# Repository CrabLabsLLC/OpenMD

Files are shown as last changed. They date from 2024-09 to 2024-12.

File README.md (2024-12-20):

# OpenMD

An Open Source Versatile Motor Driver powered by GaN

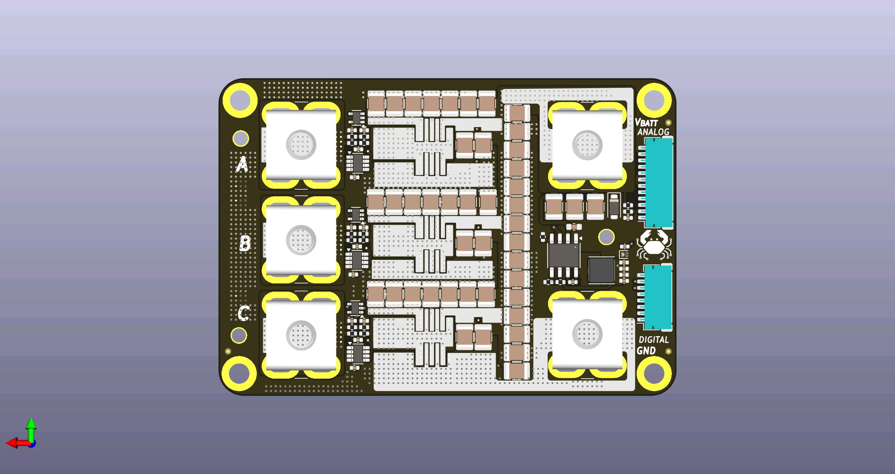
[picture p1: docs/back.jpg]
Back

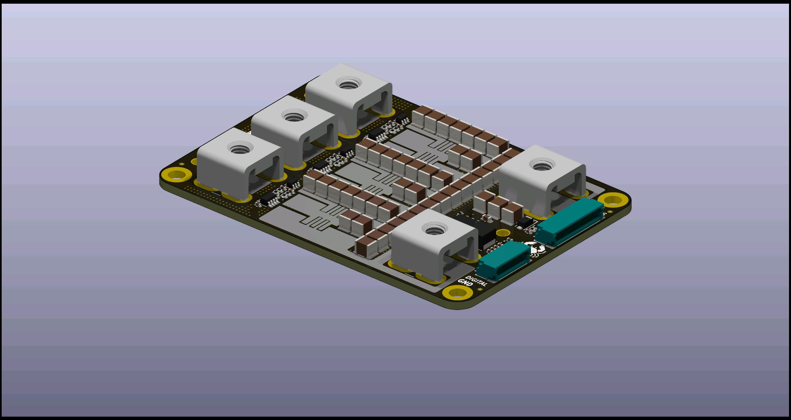
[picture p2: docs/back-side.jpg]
Side Back

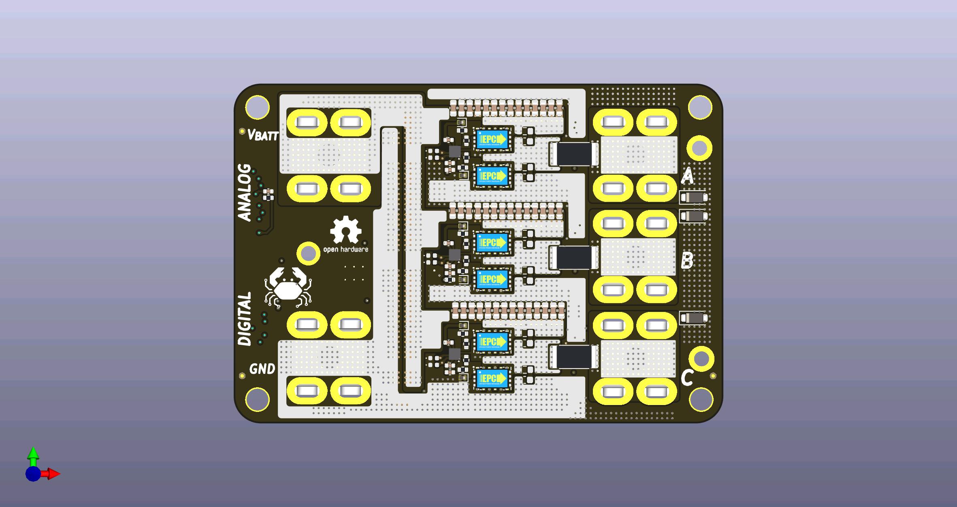
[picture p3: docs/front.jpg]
Front

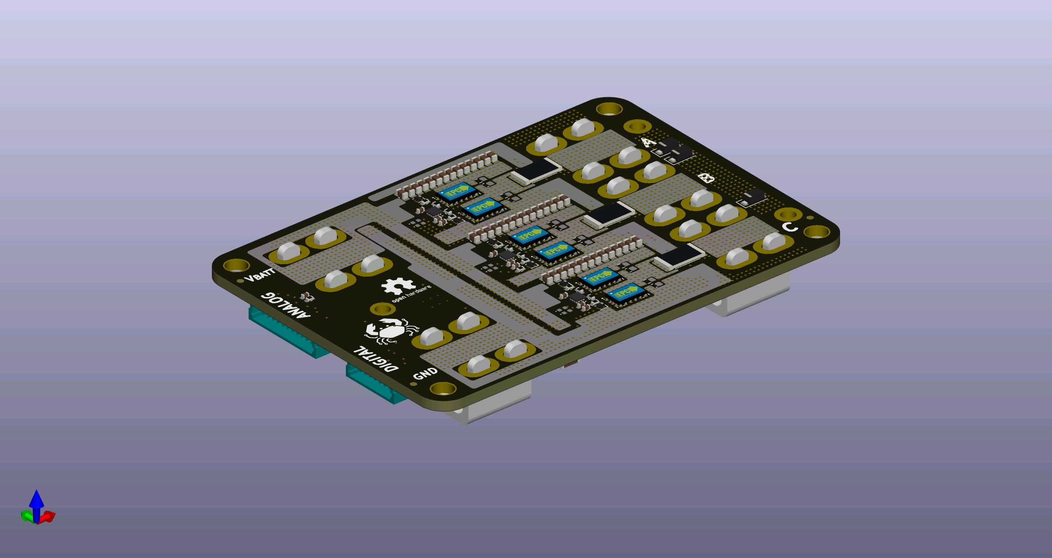
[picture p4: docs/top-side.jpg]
Side Front


## Authors

[Orion Serup](orion@crablabs.io)

## Licensing

This project is licensed under the CERN Open Hardware License Version 2 - Weakly Reciprocal.

Different licensing can be provided for a nominal fee to allow for private spins of the design, contact the authors for more information on cost and license options.

## Operational Parameters

These are the initial estimates for reasonable limits provided sufficient cooling and stable power.

- Operating Voltage: 7V-80V
- Operating Current: 70A
- Max Theoretical Power: 4kW
- Switching Frequency: 50kHz-150KHz

## Purchasing

As of now this product is in Beta and thus is not publicly available for sale. Pre-production units may be available for evaluation, contact the authors for more information.

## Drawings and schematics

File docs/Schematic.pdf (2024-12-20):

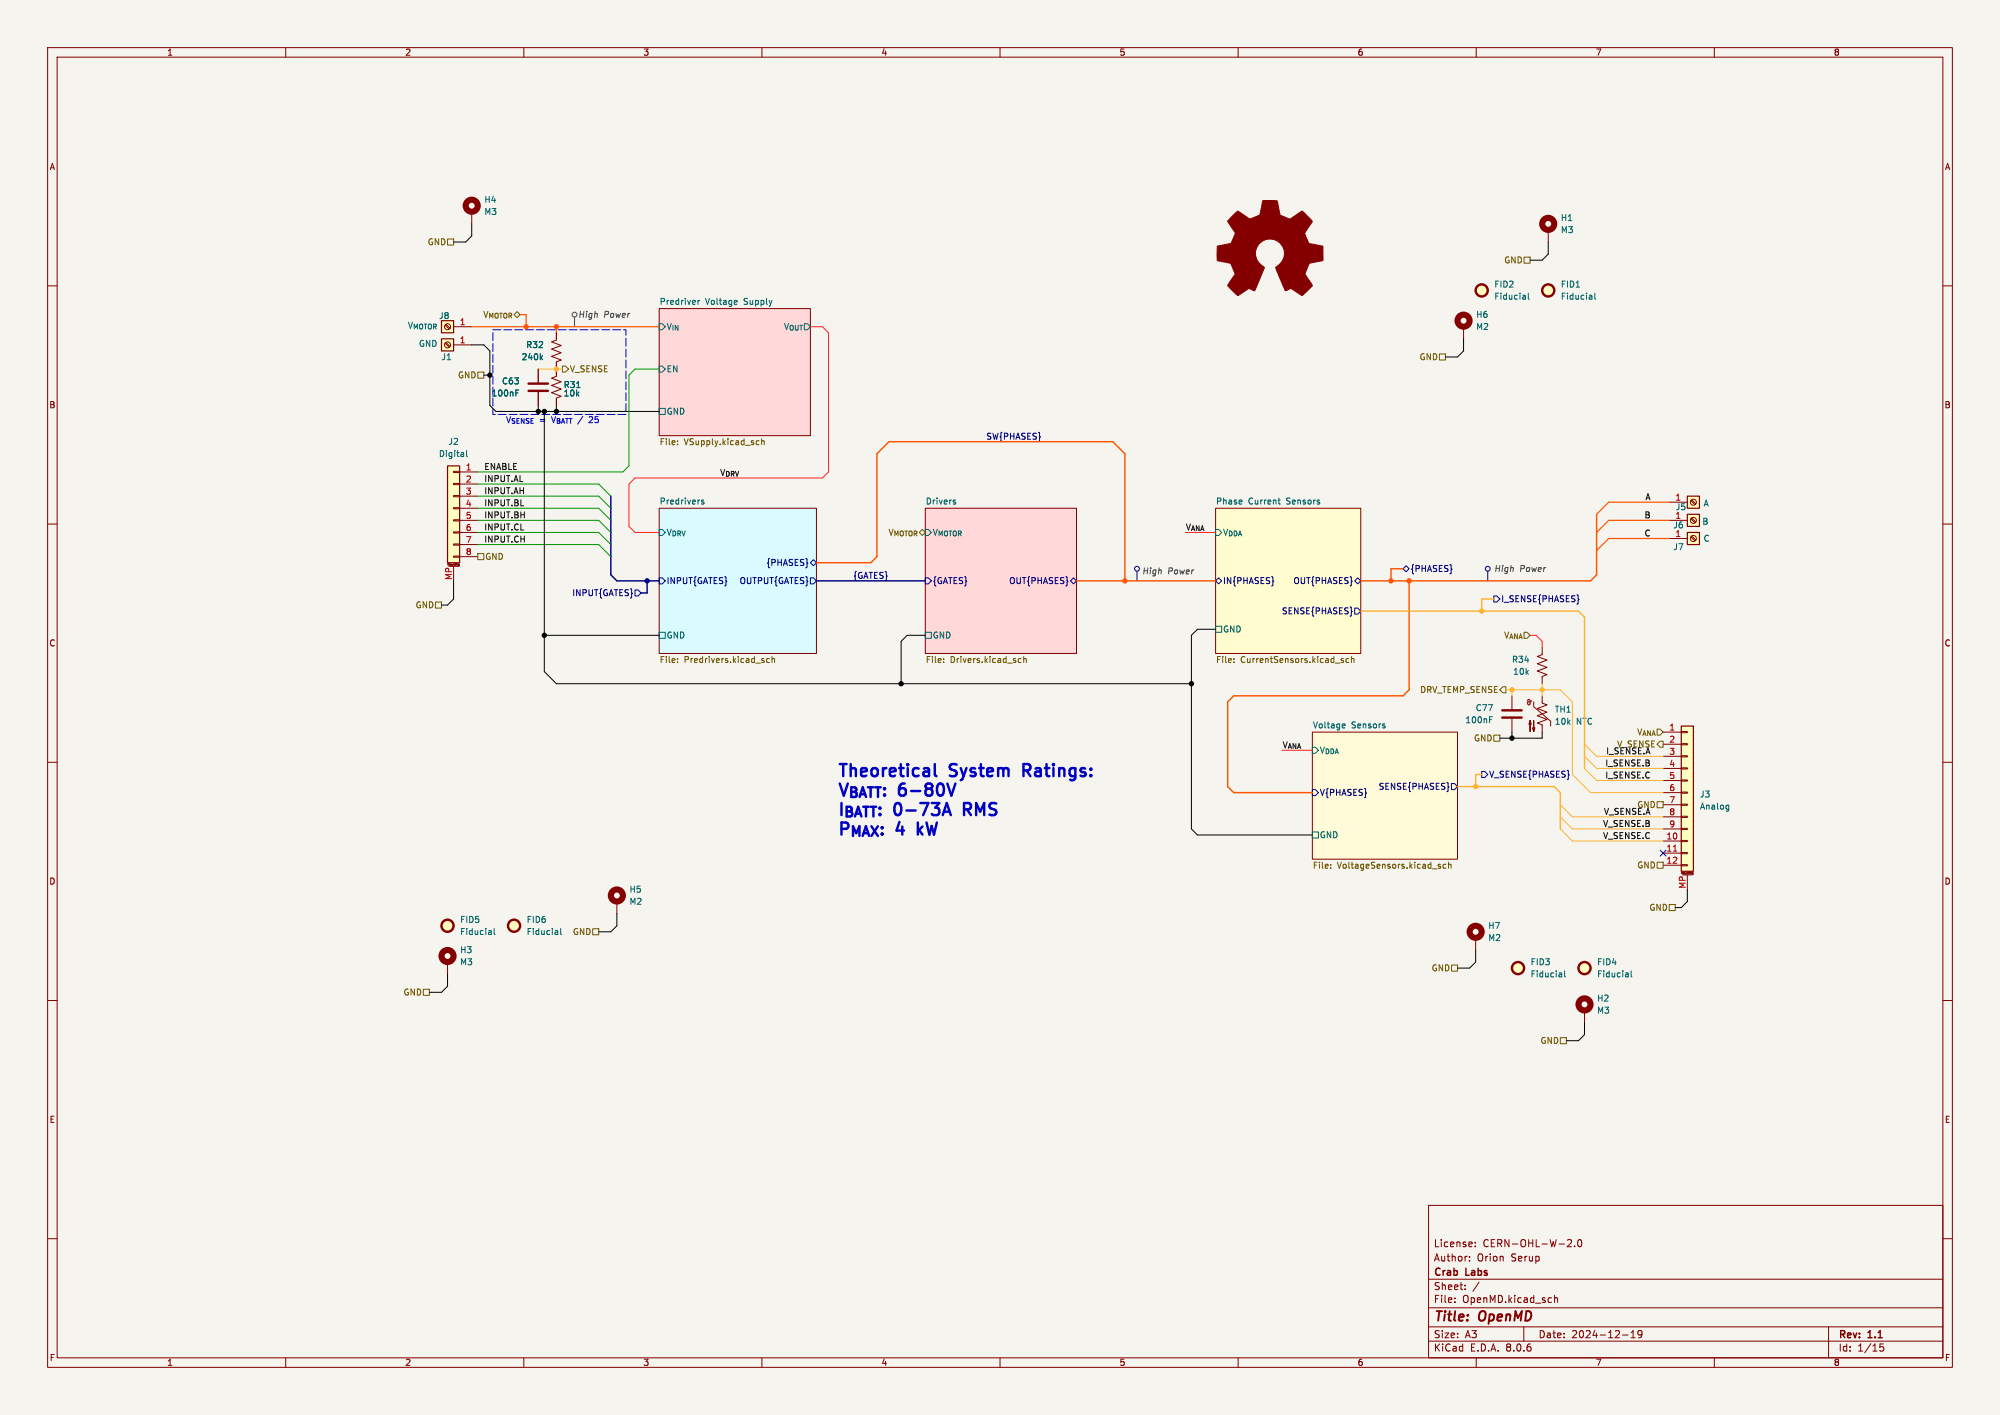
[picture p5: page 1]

Voltage Sensors File: VoltageSensors.kicad_sch

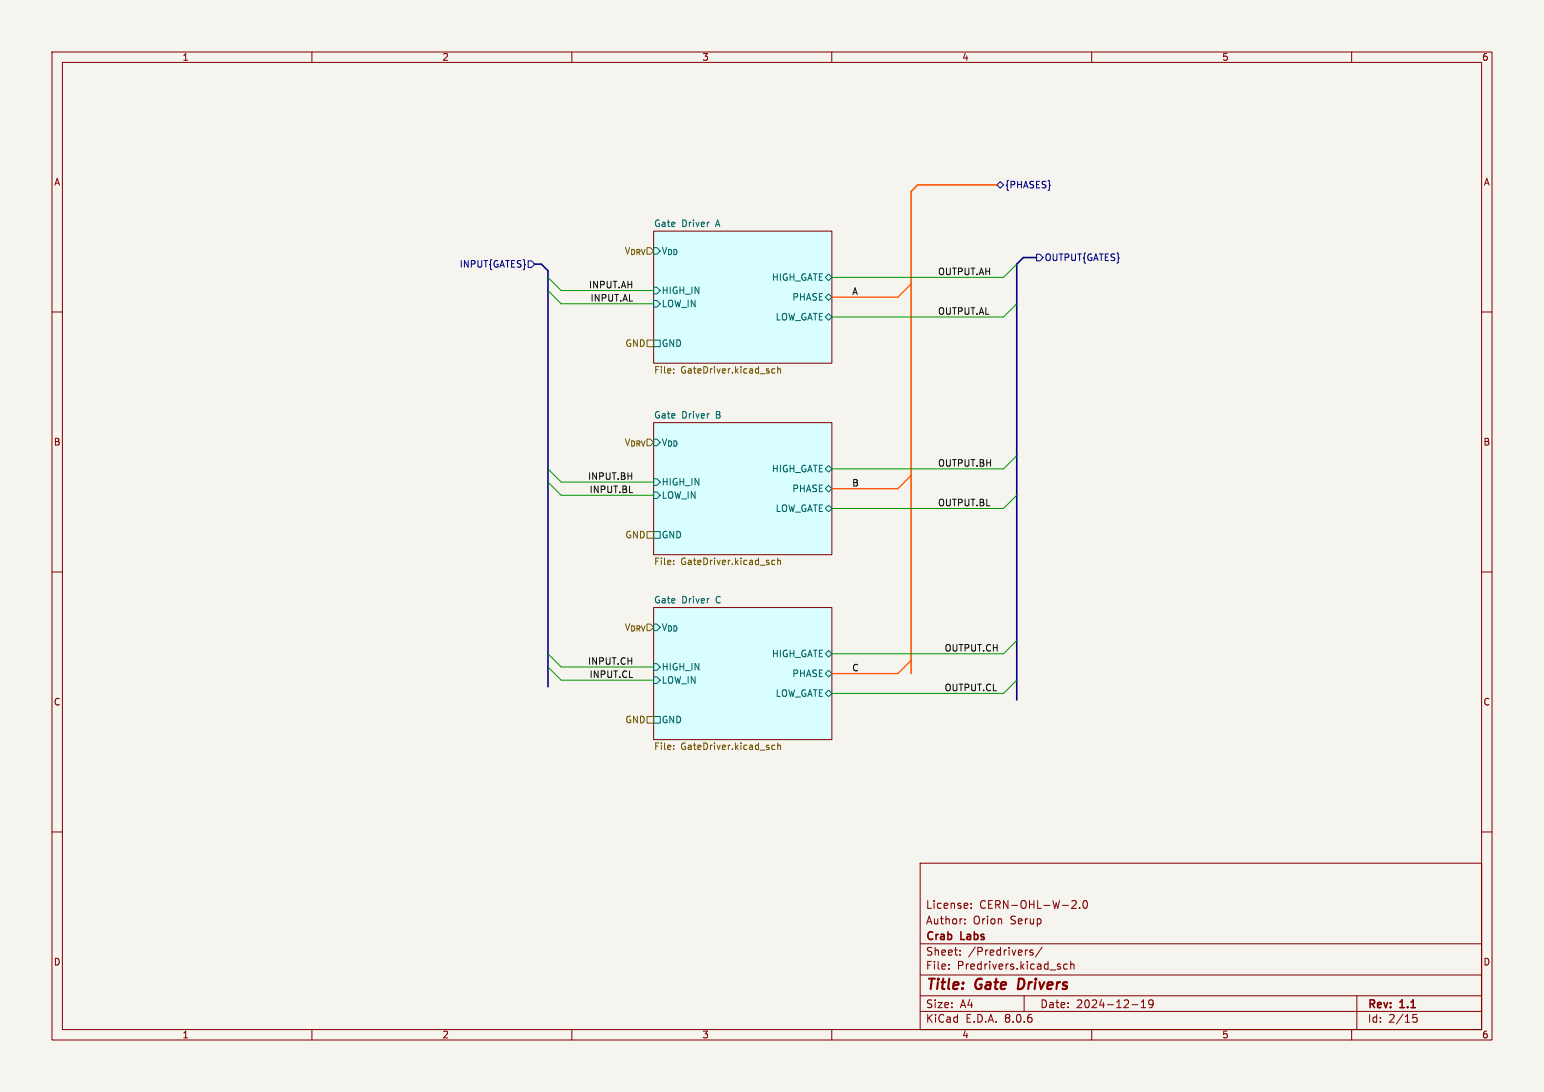
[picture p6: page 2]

OUTPUT{GATES} V_{DRV} GND GND GND

License: CERN-OHL-W-2.0 PHASE GND
LOW_IN

Id: 2/15 Title: Gate Drivers

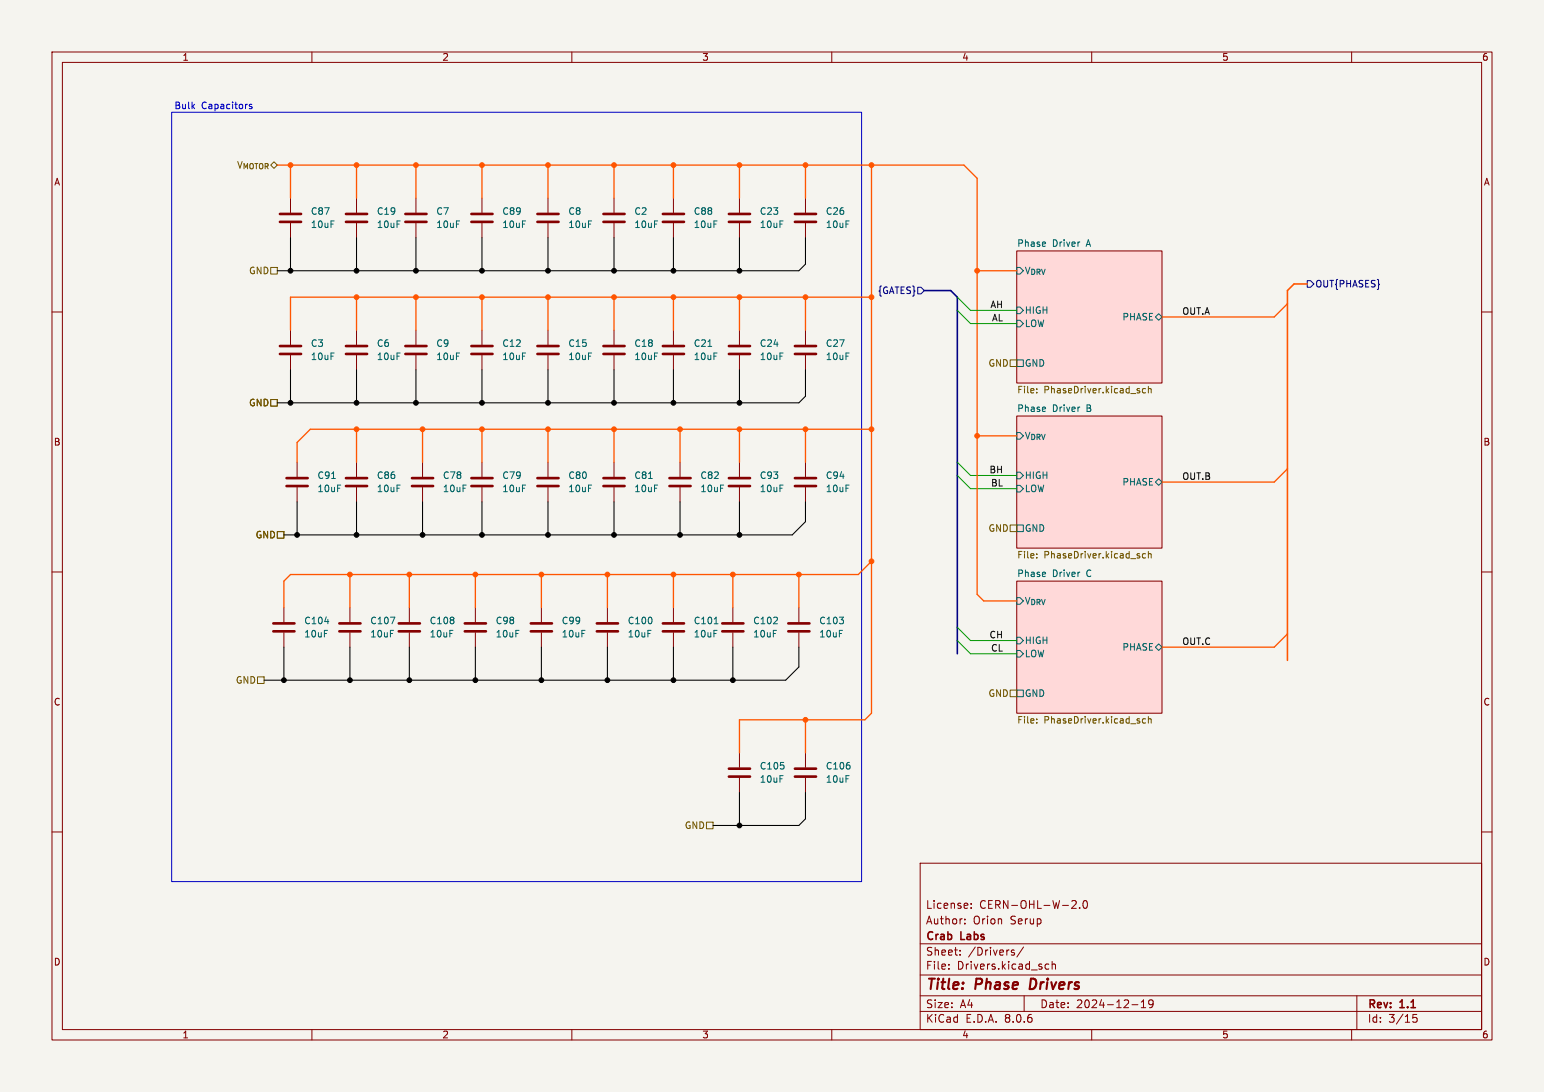
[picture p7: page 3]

File: PhaseDriver.kicad_sch HIGH
License: CERN-OHL-W-2.0 HIGH

Id: 3/15 Title: Phase Drivers

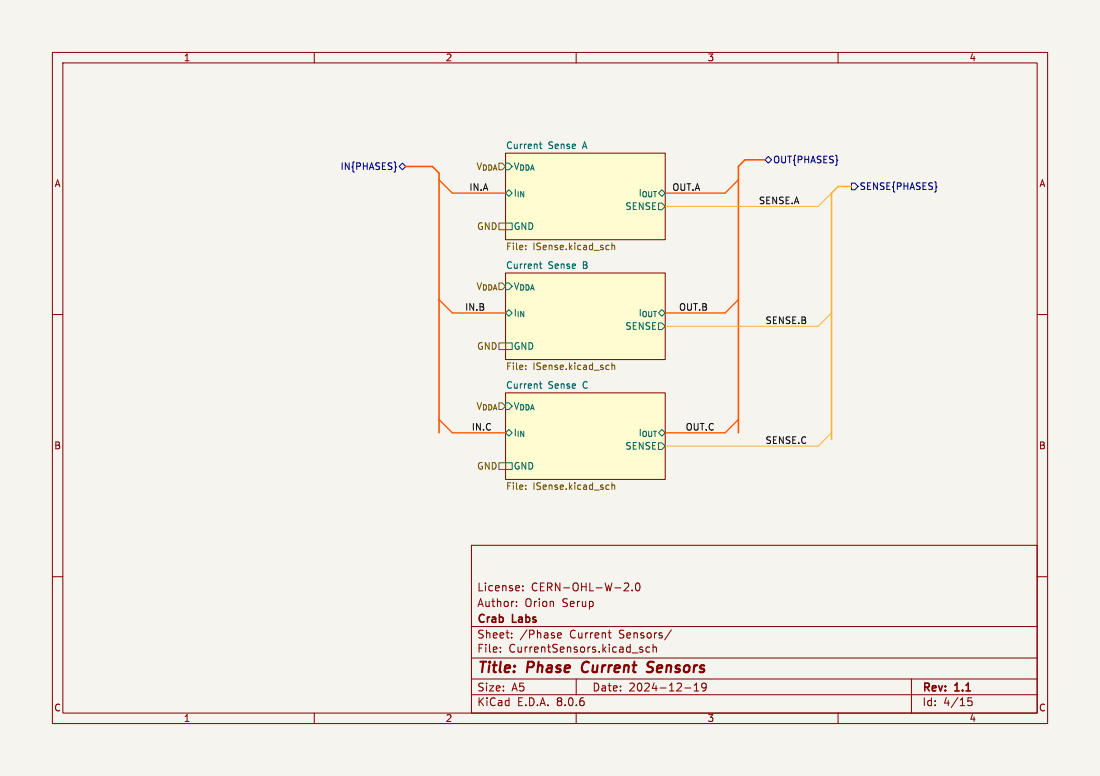
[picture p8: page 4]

License: CERN-OHL-W-2.0 GND

Id: 4/15 Title: Phase Current Sensors

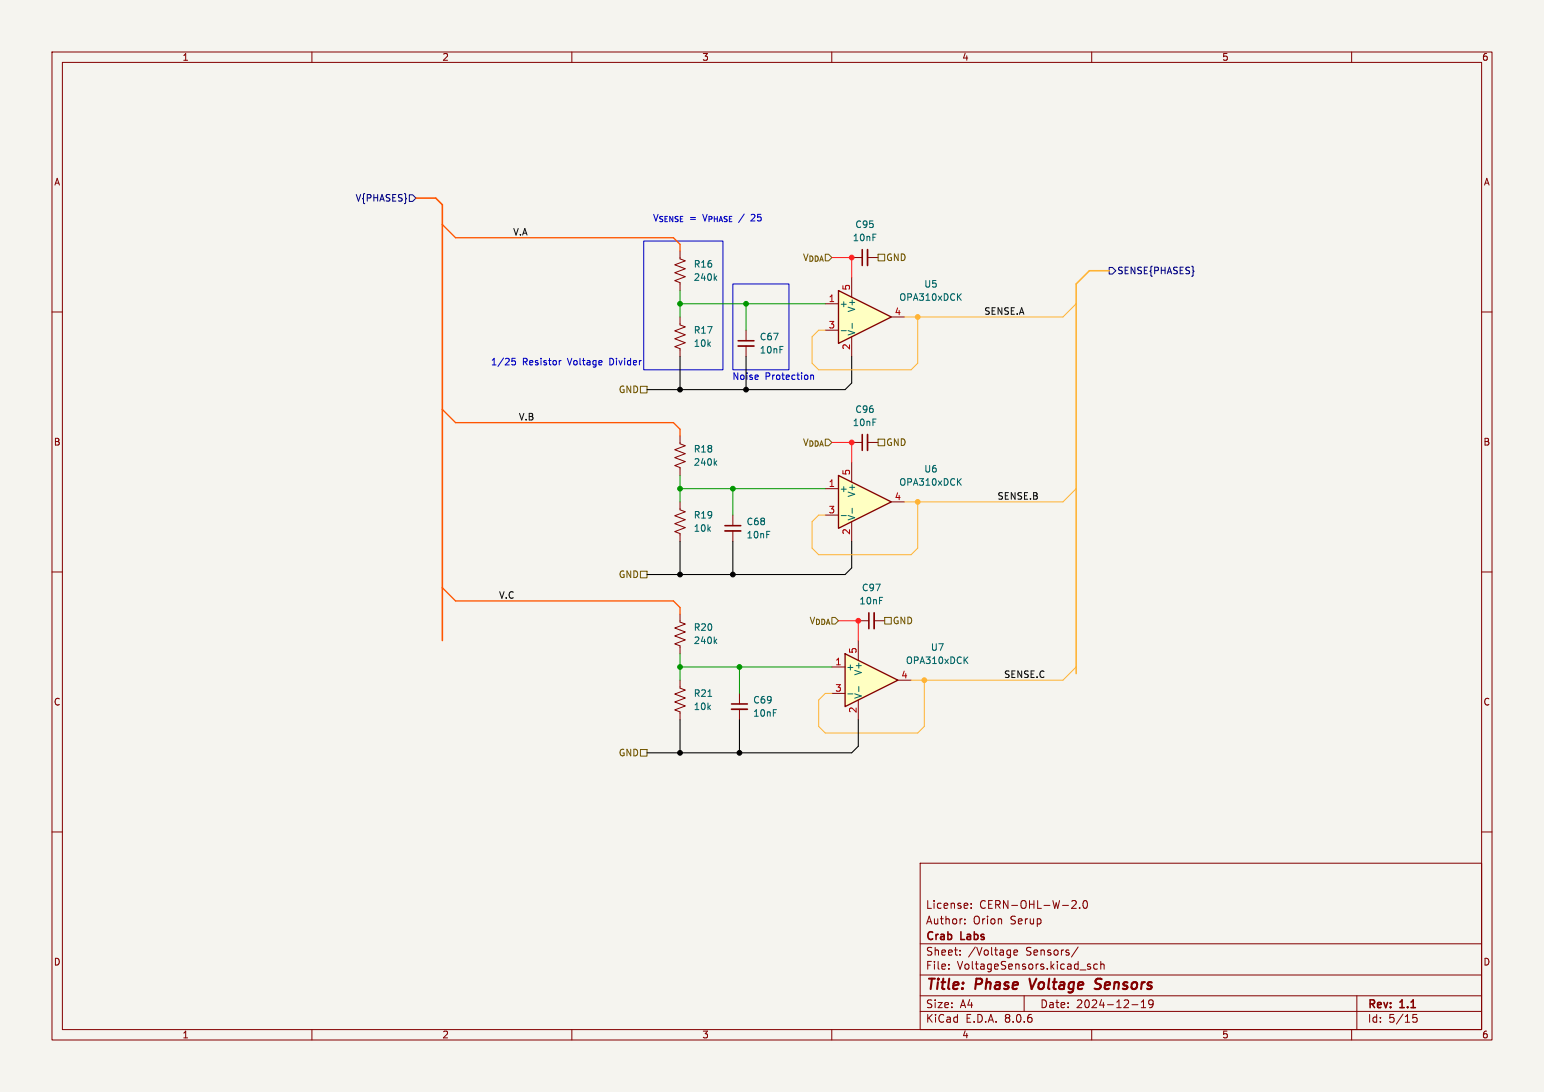
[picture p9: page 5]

Id: 5/15 Title: Phase Voltage Sensors

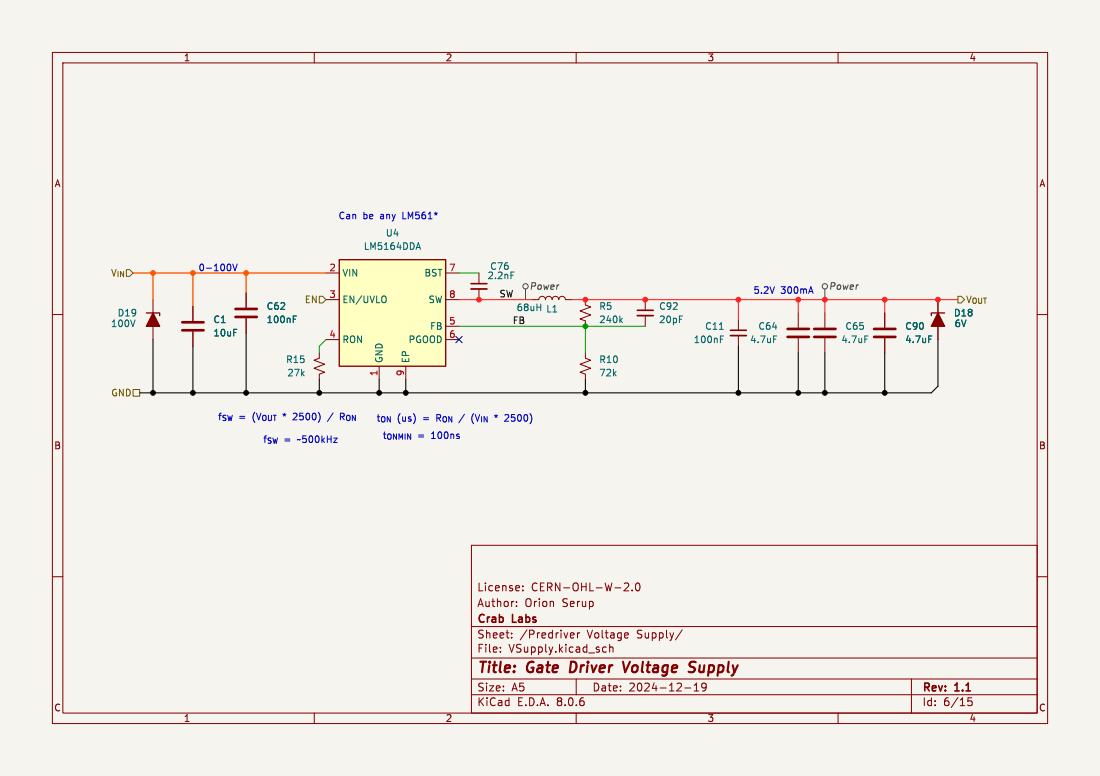
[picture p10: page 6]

1 VIN 2 EN/UVLO 3 RON 4 FB 5 PGOOD 6 BST 7 SW 8 EP

Id: 6/15 Title: Gate Driver Voltage Supply

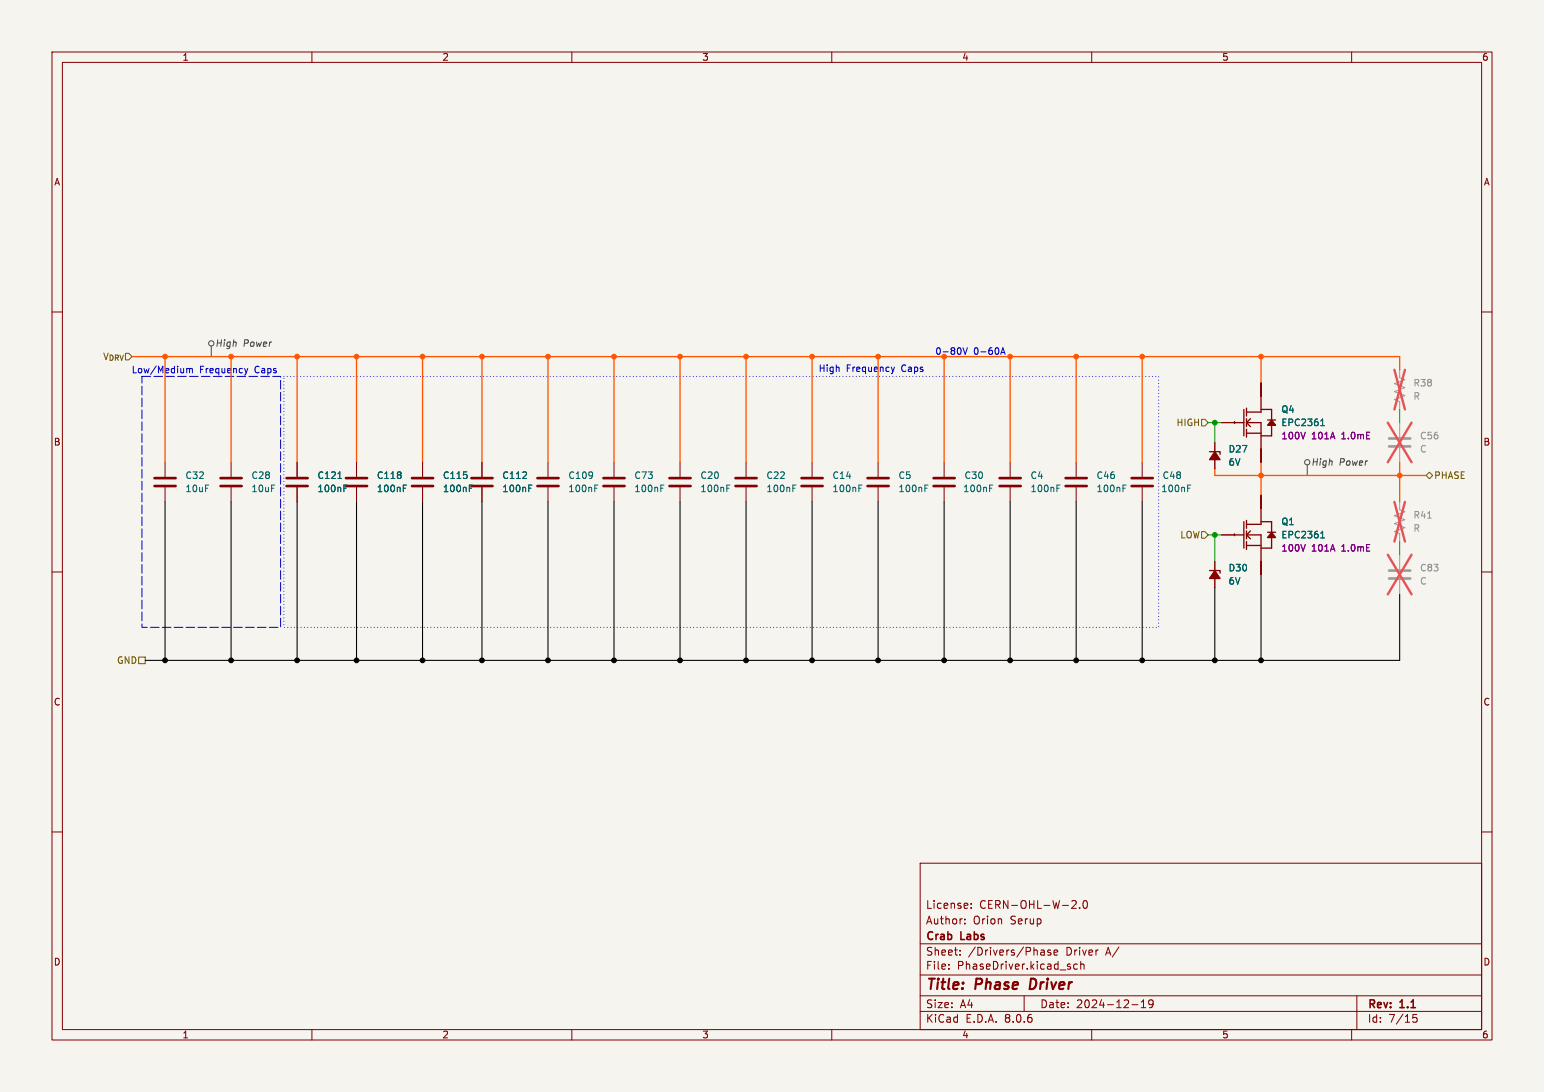
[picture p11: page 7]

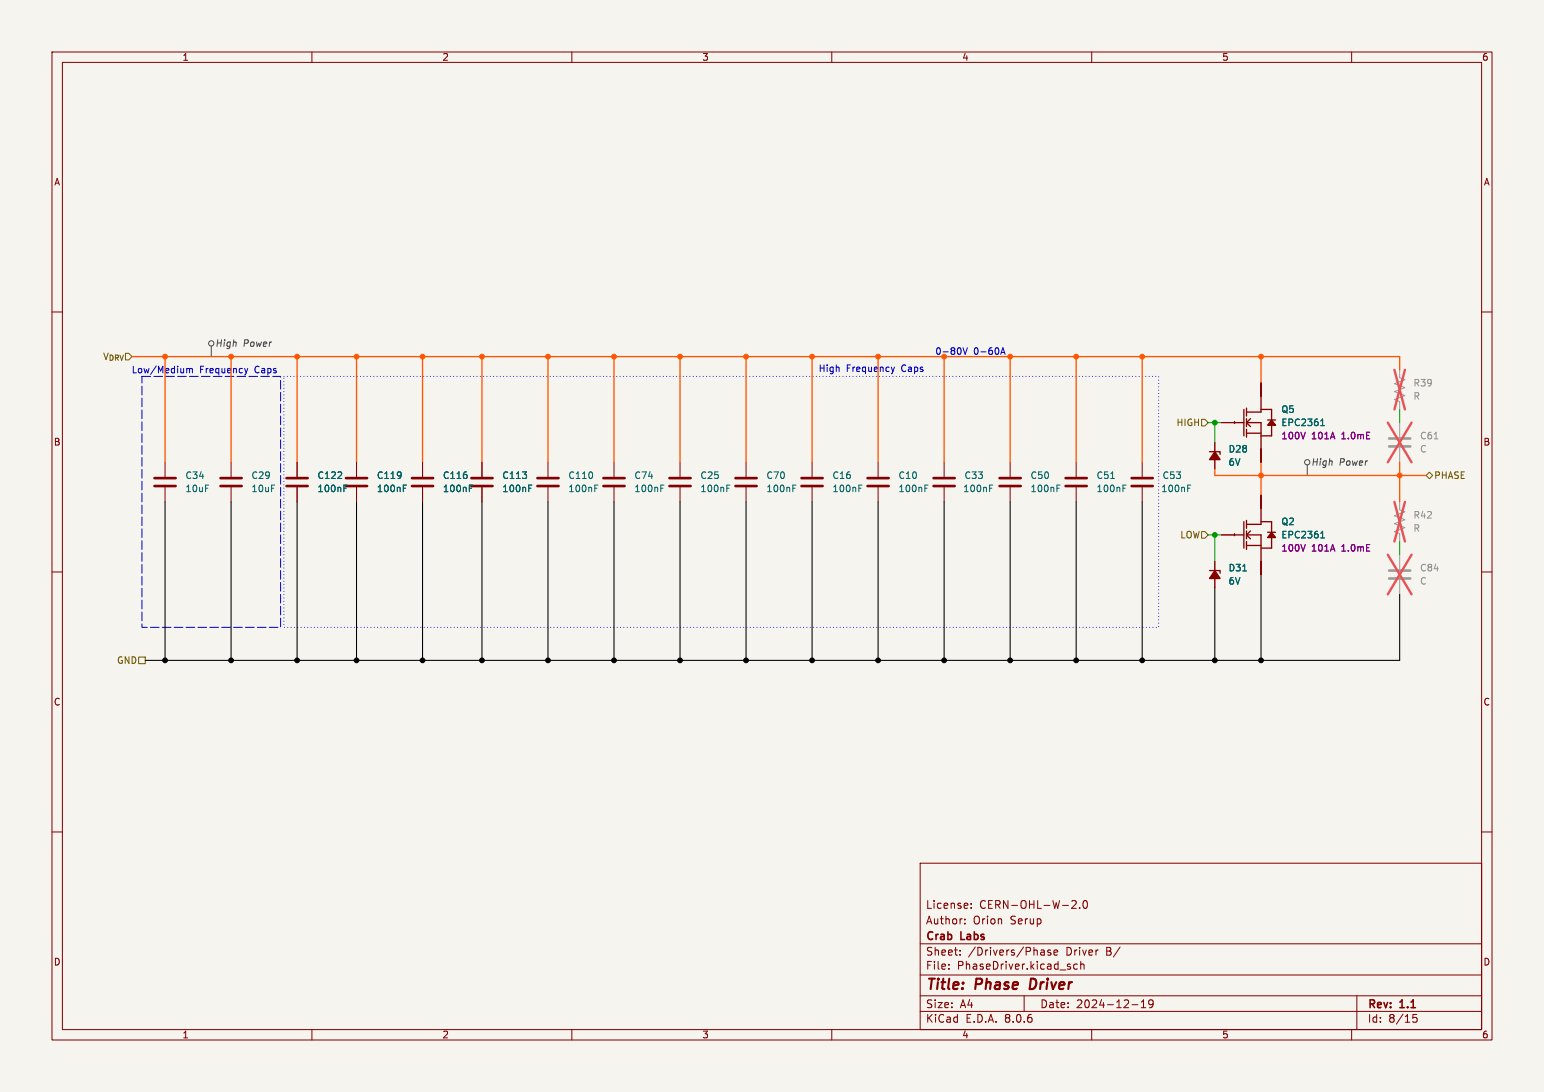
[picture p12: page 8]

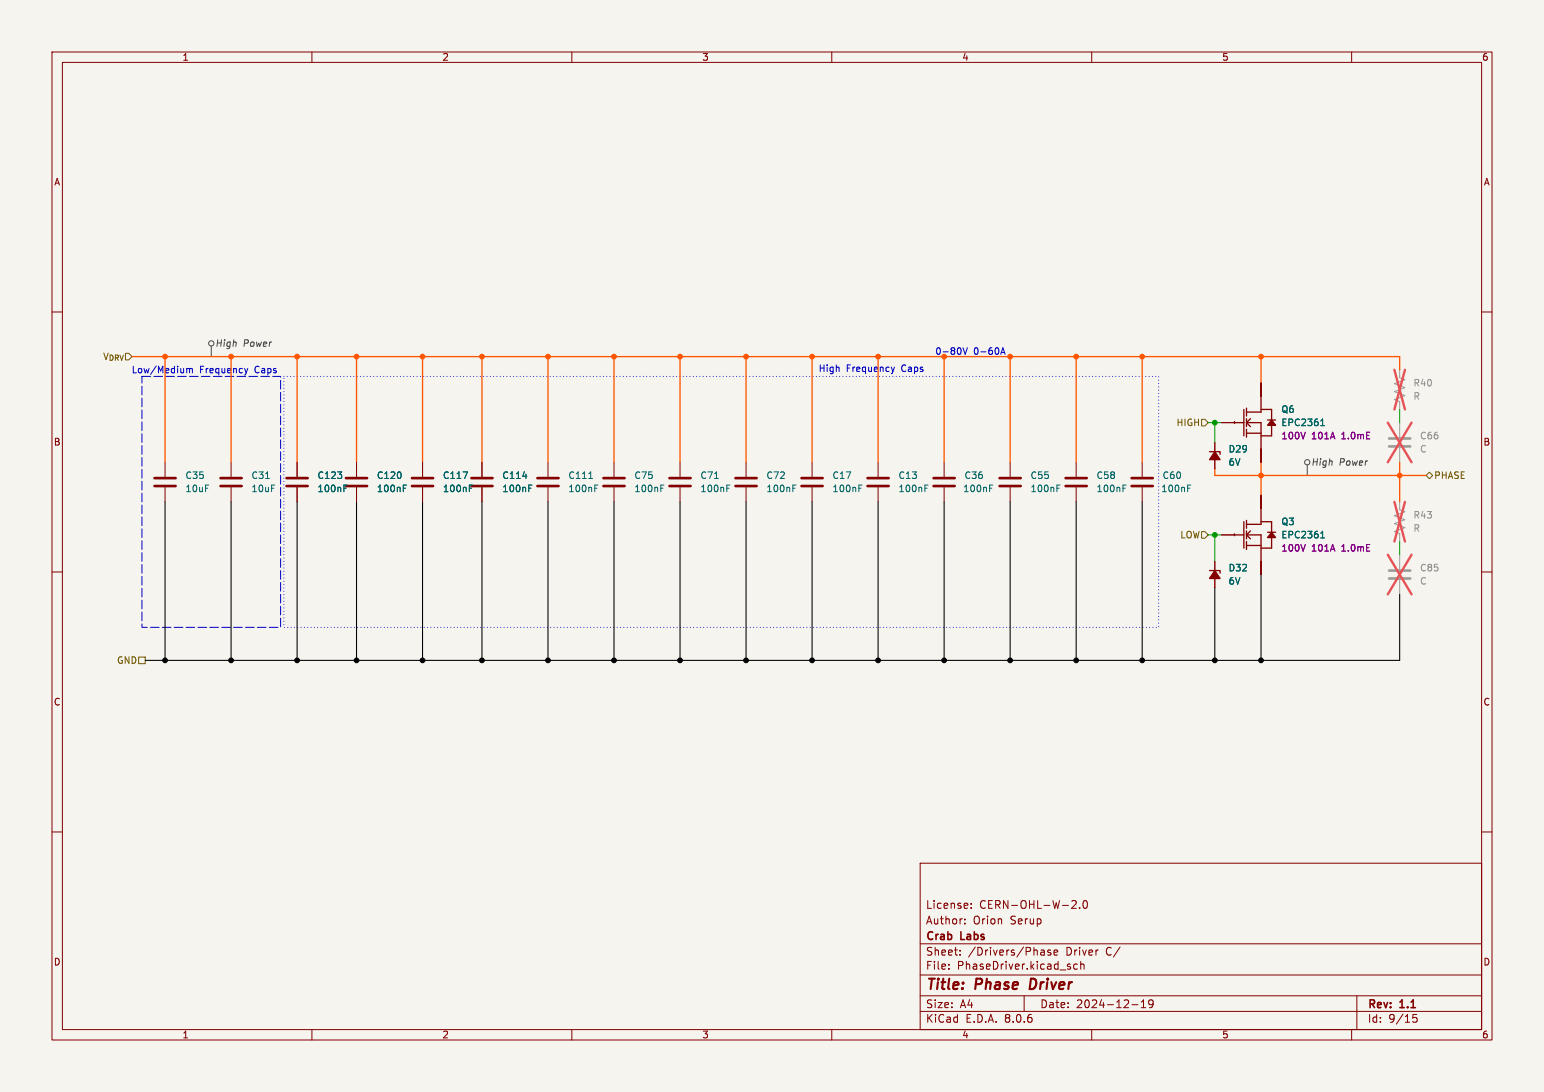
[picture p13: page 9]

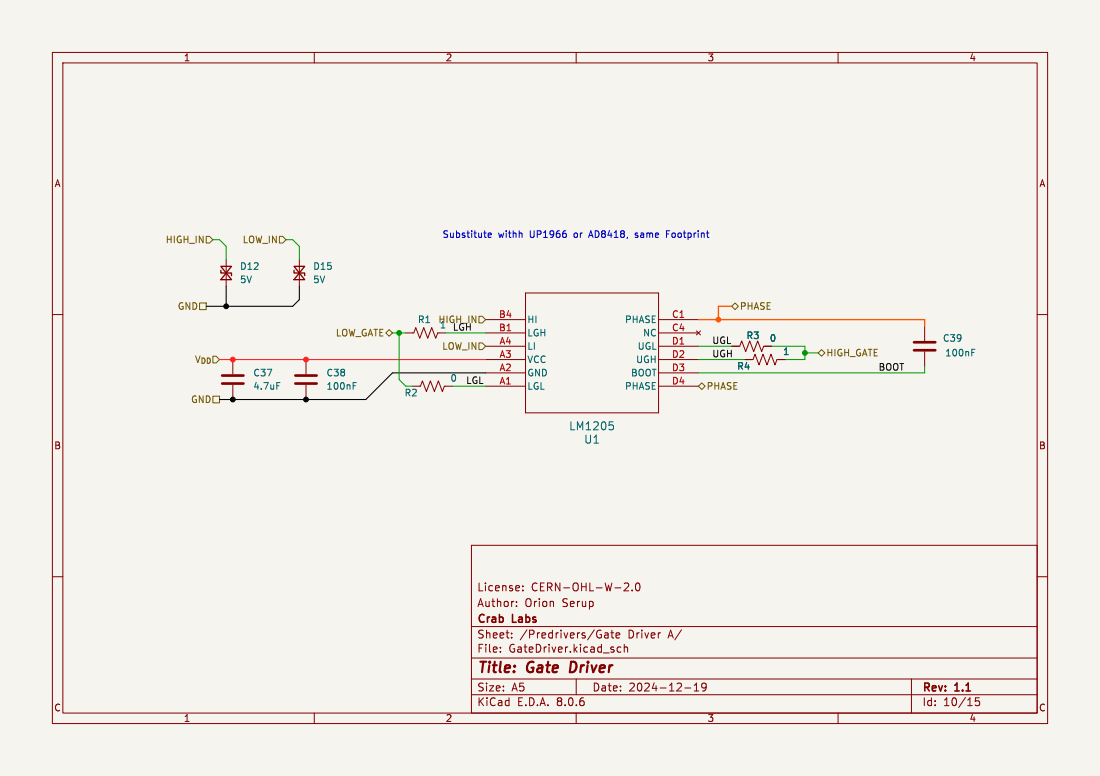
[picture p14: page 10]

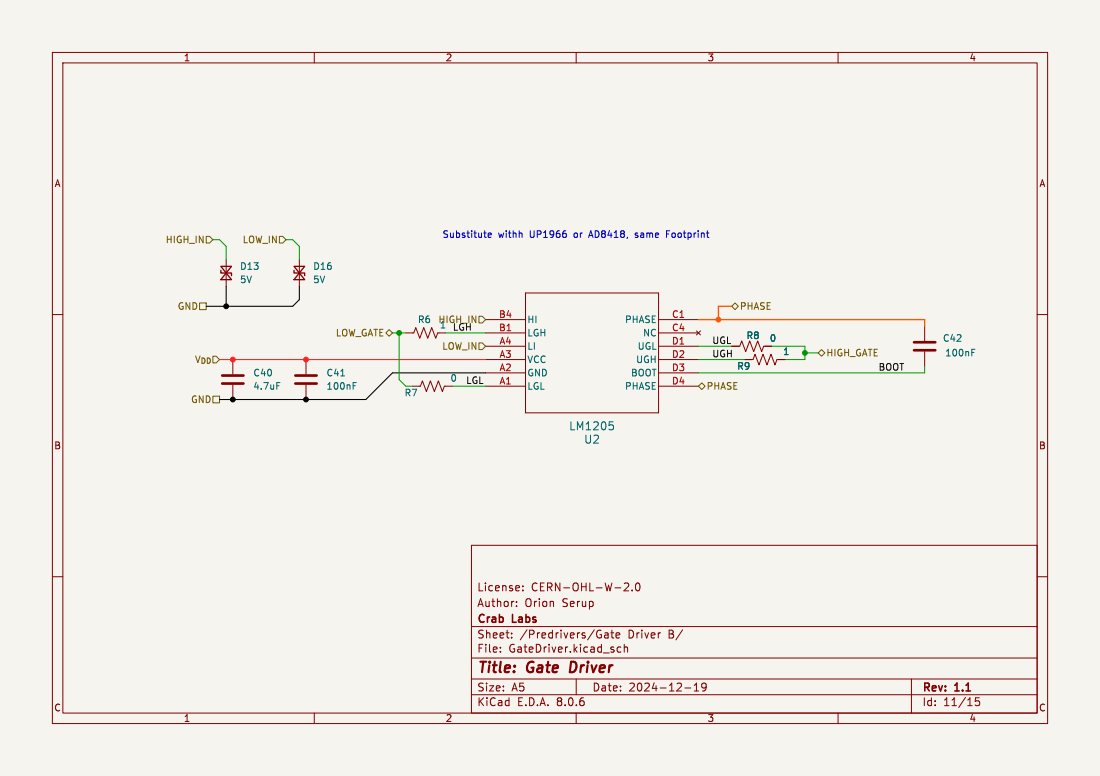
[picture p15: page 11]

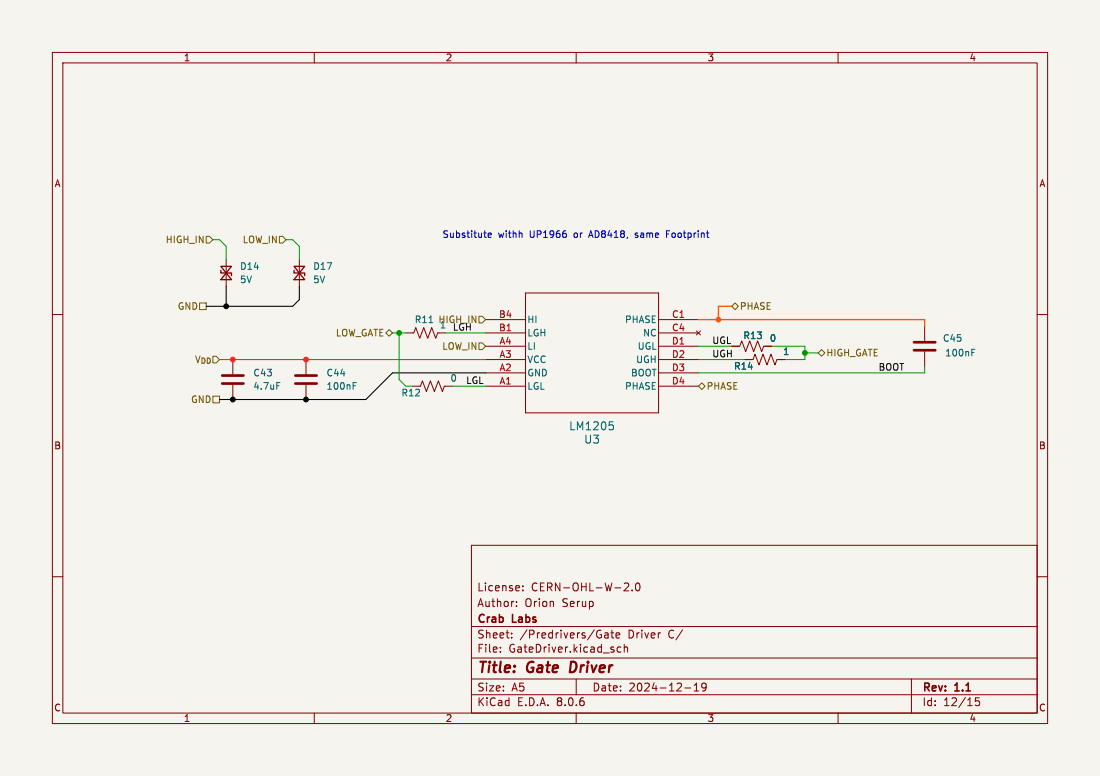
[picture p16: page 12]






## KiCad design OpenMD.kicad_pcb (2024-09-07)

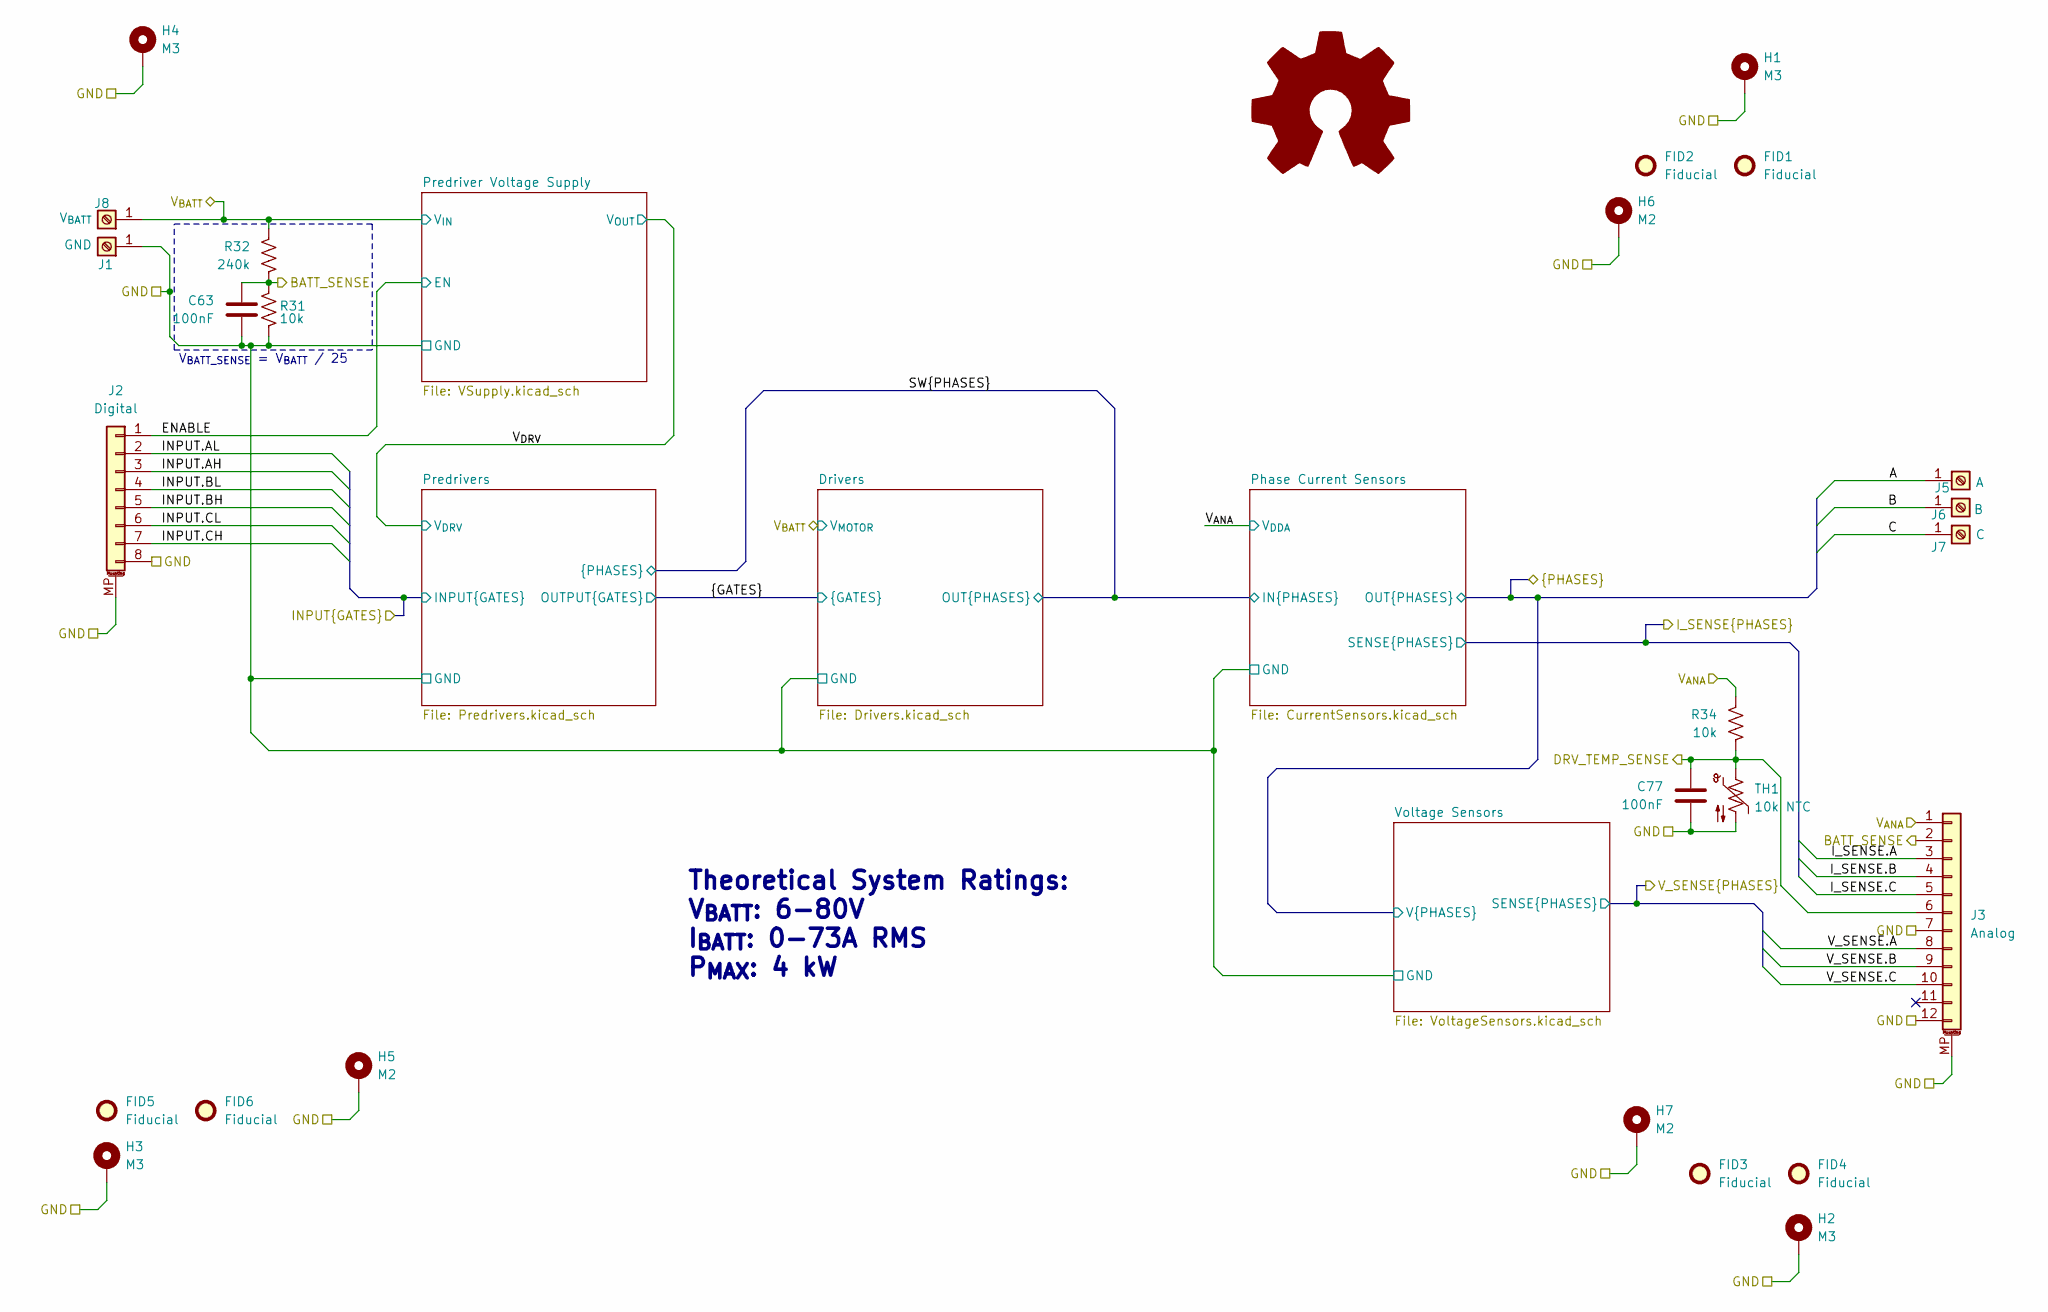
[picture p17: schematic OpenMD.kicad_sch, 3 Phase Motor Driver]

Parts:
C63, C77: 100nF; C_0402_1005Metric; Rating 5V
FID1, FID2, FID3, FID4, FID5, FID6: Fiducial; Fiducial_0.5mm_Mask1mm; Manufacturer_Part_Number N/A
H1, H2, H3, H4: M3; MountingHole_3.2mm_M3_ISO14580_Pad_TopOnly; Manufacturer_Part_Number N/A
H5: M2; MountingHole_2.2mm_M2_ISO7380_Pad_TopOnly; Manufacturer_Part_Number N/A
H6, H7: M2; MountingHole_2.2mm_M2_DIN965_Pad_TopOnly; Manufacturer_Part_Number N/A
J1: GND; DIP-4_252; Rating 80A; Manufacturer_Part_Number AMT0440005TH0000G
J2: Digital; JST_SH_SM08B-SRSS-TB_1x08-1MP_P1.00mm_Horizontal; Manufacturer_Part_Number SM08B-SRSS-TB(LF)(SN)
J3: Analog; JST_SH_SM12B-SRSS-TB_1x12-1MP_P1.00mm_Horizontal; Rating 1A; Manufacturer_Part_Number SM12B-SRSS-TB(LF)(SN)
J5: A; DIP-4_252; Rating 80A; Manufacturer_Part_Number AMT0440005TH0000G
J6: B; DIP-4_252; Rating 80A; Manufacturer_Part_Number AMT0440005TH0000G
J7: C; DIP-4_252; Rating 80A; Manufacturer_Part_Number AMT0440005TH0000G
J8: V_{BATT}; DIP-4_252; Rating 80A; Manufacturer_Part_Number AMT0440005TH0000G
R31, R34: 10k; R_0402_1005Metric; Rating 100mW; Manufacturer_Part_Number SCR0603J10K
R32: 240k; R_0402_1005Metric; Rating 100mW; Manufacturer_Part_Number RTT03304JTP
SYM1: Logo_Open_Hardware_Large; OSHW-Symbol_8.9x8mm_SilkScreen; Manufacturer_Part_Number N/A
TH1: 10k NTC; R_0402_1005Metric; Rating 100mW; Manufacturer_Part_Number KNTC0603/10KJ3950

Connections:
/A: J5.1; also elsewhere on the board
/B: J6.1; also elsewhere on the board
/BATT_SENSE: C63.1, J3.2, R31.1, R32.2
/C: J7.1; also elsewhere on the board
/DRV_TEMP_SENSE: C77.1, J3.6, R34.2, TH1.1
/ENABLE: J2.1; also elsewhere on the board
/GND: C63.2, C77.2, H1.1, H2.1, H3.1, H4.1, H5.1, H6.1, H7.1, J1.1, J2.8, J2.MP (MountPin), J3.7, J3.12, J3.MP (MountPin), R31.2, TH1.2; also elsewhere on the board
/INPUT.AH: J2.3; also elsewhere on the board
/INPUT.AL: J2.2; also elsewhere on the board
/INPUT.BH: J2.5; also elsewhere on the board
/INPUT.BL: J2.4; also elsewhere on the board
/INPUT.CH: J2.7; also elsewhere on the board
/INPUT.CL: J2.6; also elsewhere on the board
/I_SENSE.A: J3.3; also elsewhere on the board
/I_SENSE.B: J3.4; also elsewhere on the board
/I_SENSE.C: J3.5; also elsewhere on the board
/V_SENSE.A: J3.8; also elsewhere on the board
/V_SENSE.B: J3.9; also elsewhere on the board
/V_SENSE.C: J3.10; also elsewhere on the board
/V_{ANA}: J3.1, R34.1; also elsewhere on the board
/V_{BATT}: J8.1, R32.1; also elsewhere on the board

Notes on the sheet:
V_{BATT_SENSE} = V_{BATT} / 25
Theoretical System Ratings: V_{BATT}: 6-80V I_{BATT}: 0-73A RMS P_{MAX}: 4 kW

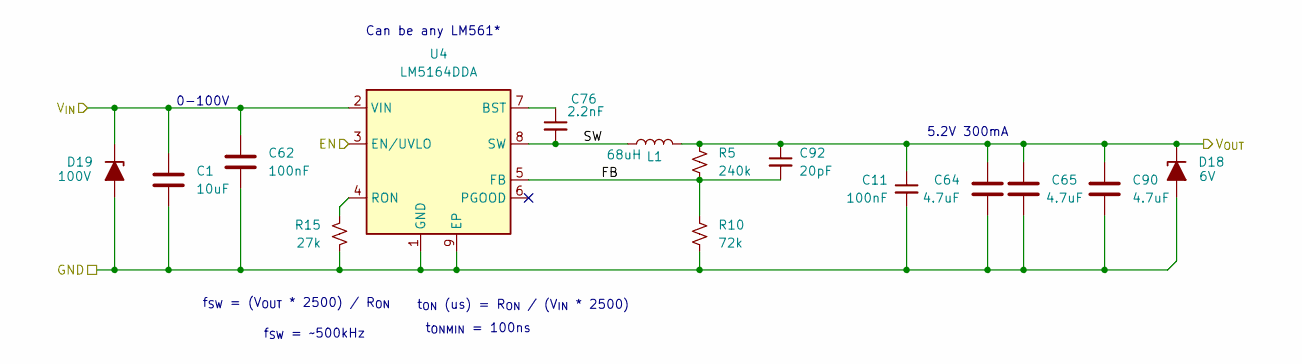
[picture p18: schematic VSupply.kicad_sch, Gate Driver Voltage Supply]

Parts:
C1: 10uF; C_1210_3225Metric; Rating 100V; Manufacturer_Part_Number FS32X475K101EGG
C11: 100nF; C_0402_1005Metric
C62: 100nF; C_0603_1608Metric; Rating 100V; Manufacturer_Part_Number CGA0603X7R104K101JT
C64, C65, C90: 4.7uF; C_0402_1005Metric; Rating 6.3V; Manufacturer_Part_Number V475M0603X5R6R3NDT
C76: 2.2nF; C_0402_1005Metric
C92: 20pF; C_0402_1005Metric
D18: 6V; D_SOD-882; Rating 1A; Manufacturer_Part_Number MMSZ5233BS-7-F
D19: 100V; D_SOD-123F; Rating 1A; Manufacturer_Part_Number SZ4582
L1: 68uH; L_Abracon_ASPI-4030S; Rating 1A; Manufacturer_Part_Number HPC 3012BMV-220M
R5: 240k; R_0402_1005Metric
R10: 72k; R_0402_1005Metric
R15: 27k; R_0402_1005Metric
U4: LM5164DDA; HSOP-8-1EP_3.9x4.9mm_P1.27mm_EP2.41x3.1mm_ThermalVias

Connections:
/ENABLE: U4.3 (EN/UVLO); also elsewhere on the board
/GND: C1.2, C11.2, C62.2, C64.2, C65.2, C90.2, D18.2 (A), D19.2 (A), R10.2, R15.2, U4.1 (GND), U4.9 (EP); also elsewhere on the board
/Predriver Voltage Supply/FB: C92.2, R5.2, R10.1, U4.5 (FB)
/Predriver Voltage Supply/SW: C76.2, L1.1, U4.8 (SW)
/V_{BATT}: C1.1, C62.1, D19.1 (K), U4.2 (VIN); also elsewhere on the board
/V_{DRV}: C11.1, C64.1, C65.1, C90.1, C92.1, D18.1 (K), L1.2, R5.1; also elsewhere on the board
unnamed: C76.1, U4.7 (BST)
unnamed: R15.1, U4.4 (RON)

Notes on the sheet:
5.2V 300mA
t_{ONMIN} = 100ns
f_{SW} = ~500kHz
0-100V
f_{SW} = (V_{OUT} * 2500) / R_{ON}
t_{ON} (us) = R_{ON} / (V_{IN} * 2500)
Can be any LM561*

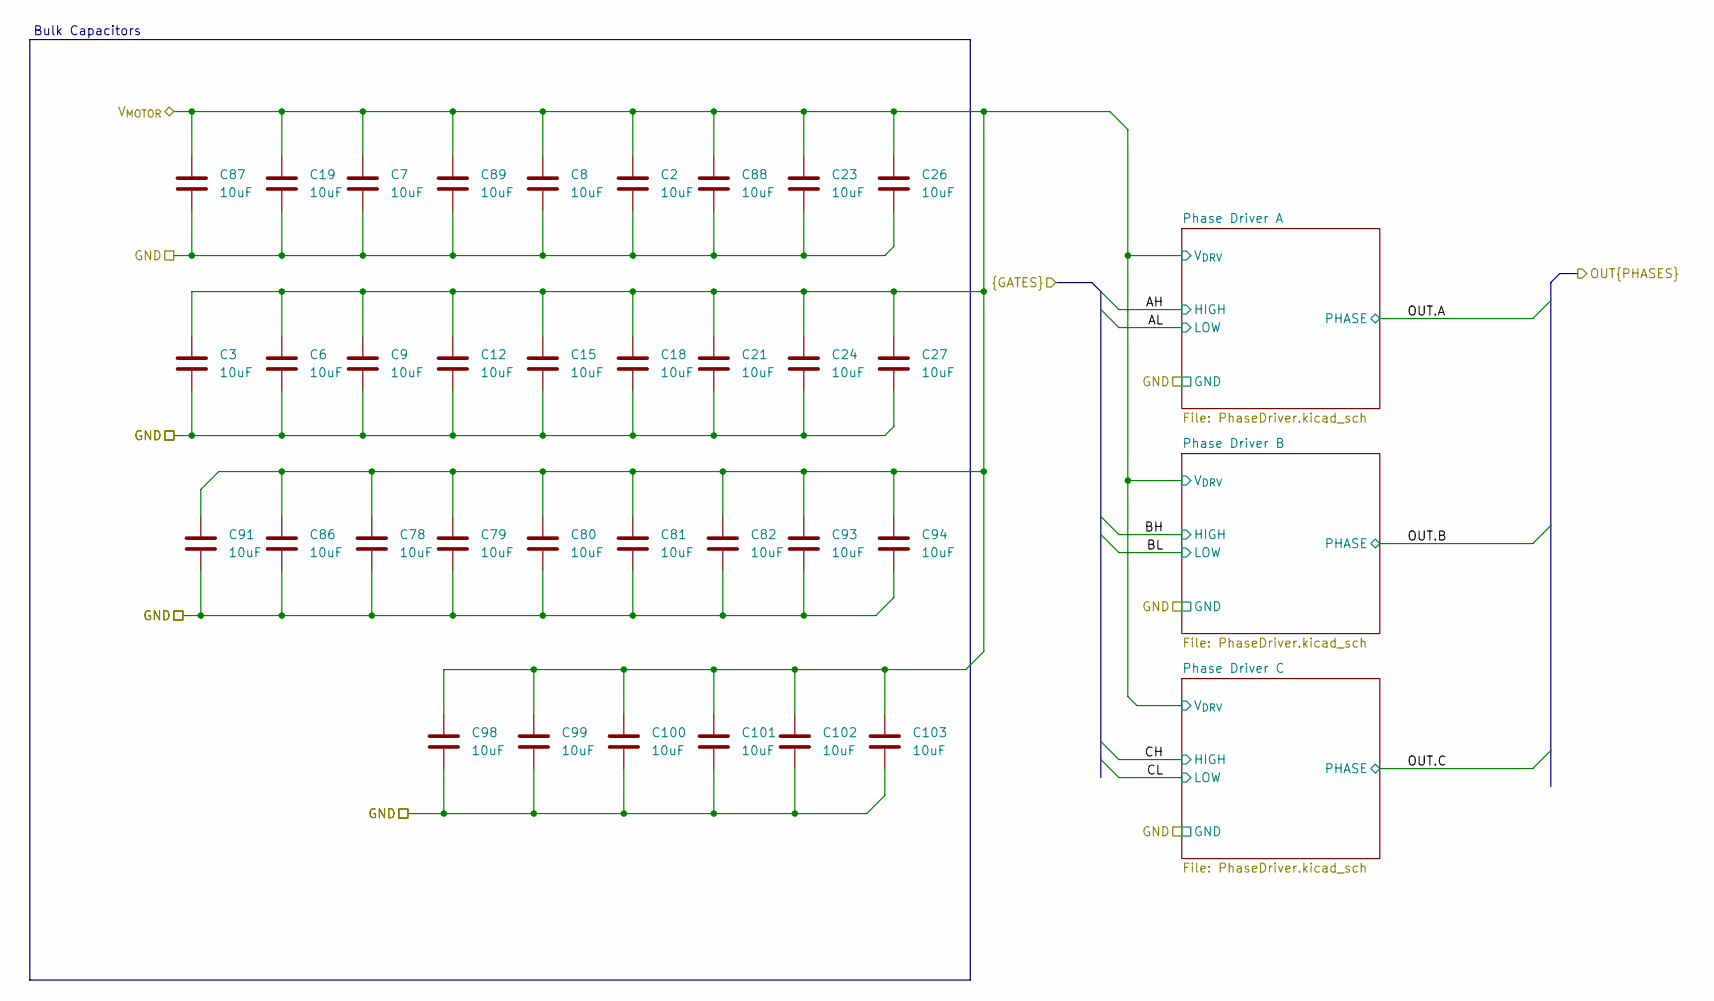
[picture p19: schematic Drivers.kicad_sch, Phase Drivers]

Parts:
C2, C3, C6, C7, C8, C9, C12, C15, C18, C19, C21, C23, C24, C26, C27, C78, C79, C80, C81, C82, C86, C87, C88, C89, C91, C93, C94, C98, C99, C100, C101, C102, C103: 10uF; C_1210_3225Metric; Rating 100V; Manufacturer_Part_Number FS32X475K101EGG

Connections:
/GND: C2.2, C3.2, C6.2, C7.2, C8.2, C9.2, C12.2, C15.2, C18.2, C19.2, C21.2, C23.2, C24.2, C26.2, C27.2, C78.2, C79.2, C80.2, C81.2, C82.2, C86.2, C87.2, C88.2, C89.2, C91.2, C93.2, C94.2, C98.2, C99.2, C100.2, C101.2, C102.2, C103.2; also elsewhere on the board
/V_{BATT}: C2.1, C3.1, C6.1, C7.1, C8.1, C9.1, C12.1, C15.1, C18.1, C19.1, C21.1, C23.1, C24.1, C26.1, C27.1, C78.1, C79.1, C80.1, C81.1, C82.1, C86.1, C87.1, C88.1, C89.1, C91.1, C93.1, C94.1, C98.1, C99.1, C100.1, C101.1, C102.1, C103.1; also elsewhere on the board

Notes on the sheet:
Bulk Capacitors

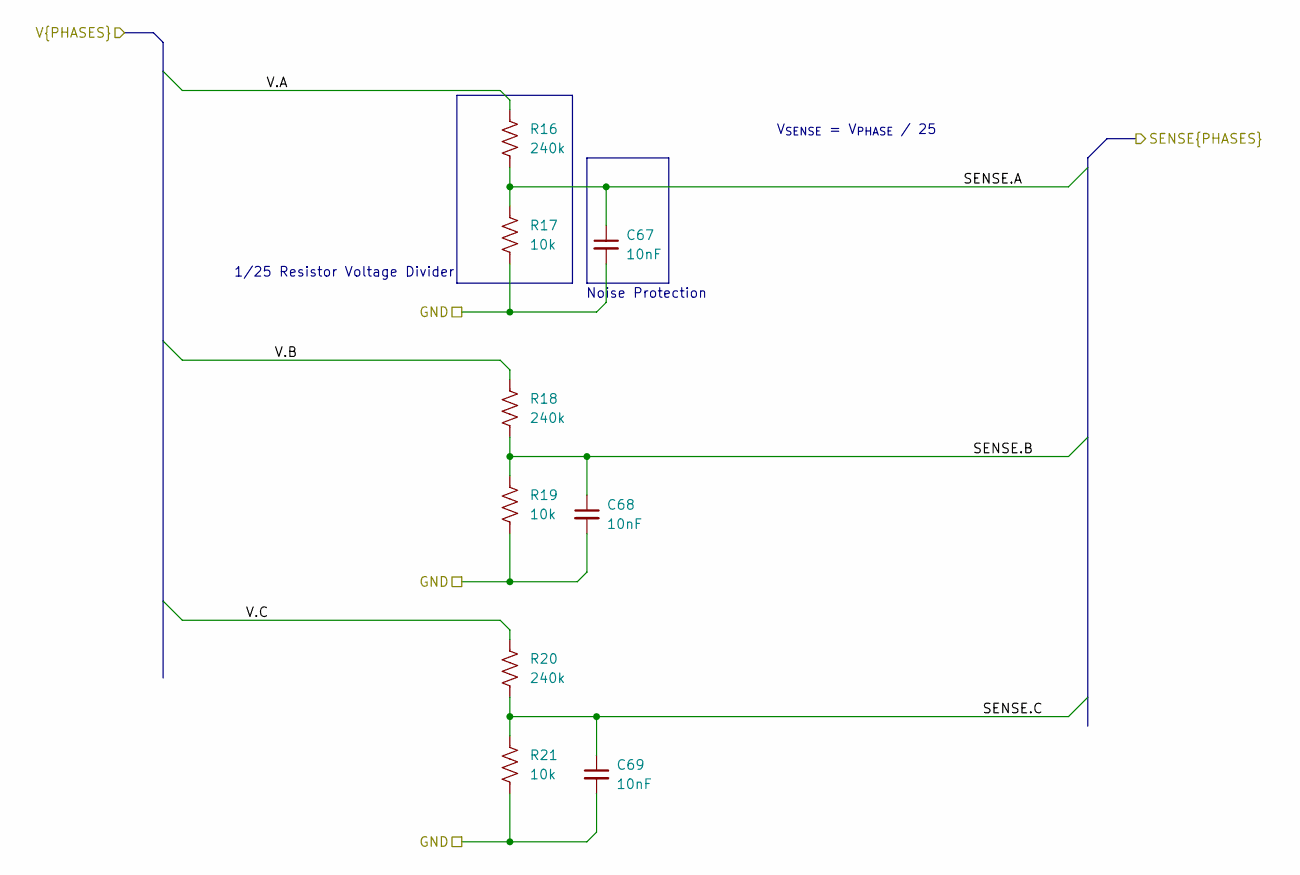
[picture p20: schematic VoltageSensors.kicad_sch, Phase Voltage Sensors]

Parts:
C67, C68, C69: 10nF; C_0402_1005Metric; Rating 5V; Manufacturer_Part_Number CSA0603X7R103K500JT
R16, R18, R20: 240k; R_0402_1005Metric; Rating 100mW; Manufacturer_Part_Number RTT03304JTP
R17, R19, R21: 10k; R_0402_1005Metric; Rating 100mW; Manufacturer_Part_Number SCR0603J10K

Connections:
/A: R16.1; also elsewhere on the board
/B: R18.1; also elsewhere on the board
/C: R20.1; also elsewhere on the board
/GND: C67.2, C68.2, C69.2, R17.2, R19.2, R21.2; also elsewhere on the board
/V_SENSE.A: C67.1, R16.2, R17.1; also elsewhere on the board
/V_SENSE.B: C68.1, R18.2, R19.1; also elsewhere on the board
/V_SENSE.C: C69.1, R20.2, R21.1; also elsewhere on the board

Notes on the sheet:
Noise Protection
1/25 Resistor Voltage Divider
V_{SENSE} = V_{PHASE} / 25

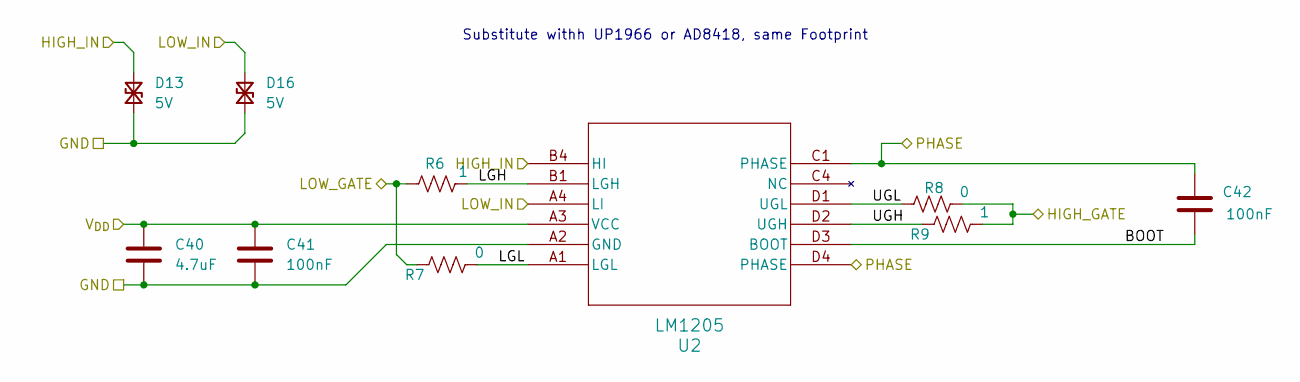
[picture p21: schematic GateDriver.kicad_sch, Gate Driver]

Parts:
C40: 4.7uF; C_0402_1005Metric; Rating 6.3V; Manufacturer_Part_Number V475M0603X5R6R3NDT
C41, C42: 100nF; C_0402_1005Metric; Rating 6.3V; Manufacturer_Part_Number CGA0603X7R104K500JT
D13, D16: 5V; D_0402_1005Metric; Rating 1A; Manufacturer_Part_Number 0603ESDA-05N
R6, R9: 1; R_0402_1005Metric; Rating 100mW; Manufacturer_Part_Number FRC0603J1R0 TS
R7, R8: 0; R_0402_1005Metric; Rating 100mW; Manufacturer_Part_Number SCR0603J0R
U2: LM1205; WLCSP1.6x1.6-12B_ECC; Rating 85V; Manufacturer_Part_Number UP1966E

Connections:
/BH: R8.2, R9.2; also elsewhere on the board
/BL: R6.2, R7.1; also elsewhere on the board
/GND: C40.2, C41.2, D13.1 (A1), D16.1 (A1), U2.A2 (GND); also elsewhere on the board
/INPUT.BH: D13.2 (A2), U2.B4 (HI); also elsewhere on the board
/INPUT.BL: D16.2 (A2), U2.A4 (LI); also elsewhere on the board
/Predrivers/Gate Driver B/BOOT: C42.1, U2.D3 (BOOT)
/Predrivers/Gate Driver B/LGH: R6.1, U2.B1 (LGH)
/Predrivers/Gate Driver B/LGL: R7.2, U2.A1 (LGL)
/Predrivers/Gate Driver B/UGH: R9.1, U2.D2 (UGH)
/Predrivers/Gate Driver B/UGL: R8.1, U2.D1 (UGL)
/SW.B: C42.2, U2.C1 (PHASE), U2.D4 (PHASE); also elsewhere on the board
/V_{DRV}: C40.1, C41.1, U2.A3 (VCC); also elsewhere on the board

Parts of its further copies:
C37, C43: 4.7uF; C_0402_1005Metric; Rating 6.3V; Manufacturer_Part_Number V475M0603X5R6R3NDT
C38, C39, C44, C45: 100nF; C_0402_1005Metric; Rating 6.3V; Manufacturer_Part_Number CGA0603X7R104K500JT
D12, D14, D15, D17: 5V; D_0402_1005Metric; Rating 1A; Manufacturer_Part_Number 0603ESDA-05N
R1, R4, R11, R14: 1; R_0402_1005Metric; Rating 100mW; Manufacturer_Part_Number FRC0603J1R0 TS
R2, R3, R12, R13: 0; R_0402_1005Metric; Rating 100mW; Manufacturer_Part_Number SCR0603J0R
U1, U3: LM1205; WLCSP1.6x1.6-12B_ECC; Rating 85V; Manufacturer_Part_Number UP1966E

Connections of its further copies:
/AH: R3.2, R4.2; also elsewhere on the board
/AL: R1.2, R2.1; also elsewhere on the board
/CH: R13.2, R14.2; also elsewhere on the board
/CL: R11.2, R12.1; also elsewhere on the board
/GND: C37.2, C38.2, C43.2, C44.2, D12.1 (A1), D14.1 (A1), D15.1 (A1), D17.1 (A1), U1.A2 (GND), U3.A2 (GND); also elsewhere on the board
/INPUT.AH: D12.2 (A2), U1.B4 (HI); also elsewhere on the board
/INPUT.AL: D15.2 (A2), U1.A4 (LI); also elsewhere on the board
/INPUT.CH: D14.2 (A2), U3.B4 (HI); also elsewhere on the board
/INPUT.CL: D17.2 (A2), U3.A4 (LI); also elsewhere on the board
/Predrivers/Gate Driver A/BOOT: C39.1, U1.D3 (BOOT)
/Predrivers/Gate Driver A/LGH: R1.1, U1.B1 (LGH)
/Predrivers/Gate Driver A/LGL: R2.2, U1.A1 (LGL)
/Predrivers/Gate Driver A/UGH: R4.1, U1.D2 (UGH)
/Predrivers/Gate Driver A/UGL: R3.1, U1.D1 (UGL)
/Predrivers/Gate Driver C/BOOT: C45.1, U3.D3 (BOOT)
/Predrivers/Gate Driver C/LGH: R11.1, U3.B1 (LGH)
/Predrivers/Gate Driver C/LGL: R12.2, U3.A1 (LGL)
/Predrivers/Gate Driver C/UGH: R14.1, U3.D2 (UGH)
/Predrivers/Gate Driver C/UGL: R13.1, U3.D1 (UGL)
/SW.A: C39.2, U1.C1 (PHASE), U1.D4 (PHASE); also elsewhere on the board
/SW.C: C45.2, U3.C1 (PHASE), U3.D4 (PHASE); also elsewhere on the board
/V_{DRV}: C37.1, C38.1, C43.1, C44.1, U1.A3 (VCC), U3.A3 (VCC); also elsewhere on the board

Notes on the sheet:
Substitute withh UP1966 or AD8418, same Footprint

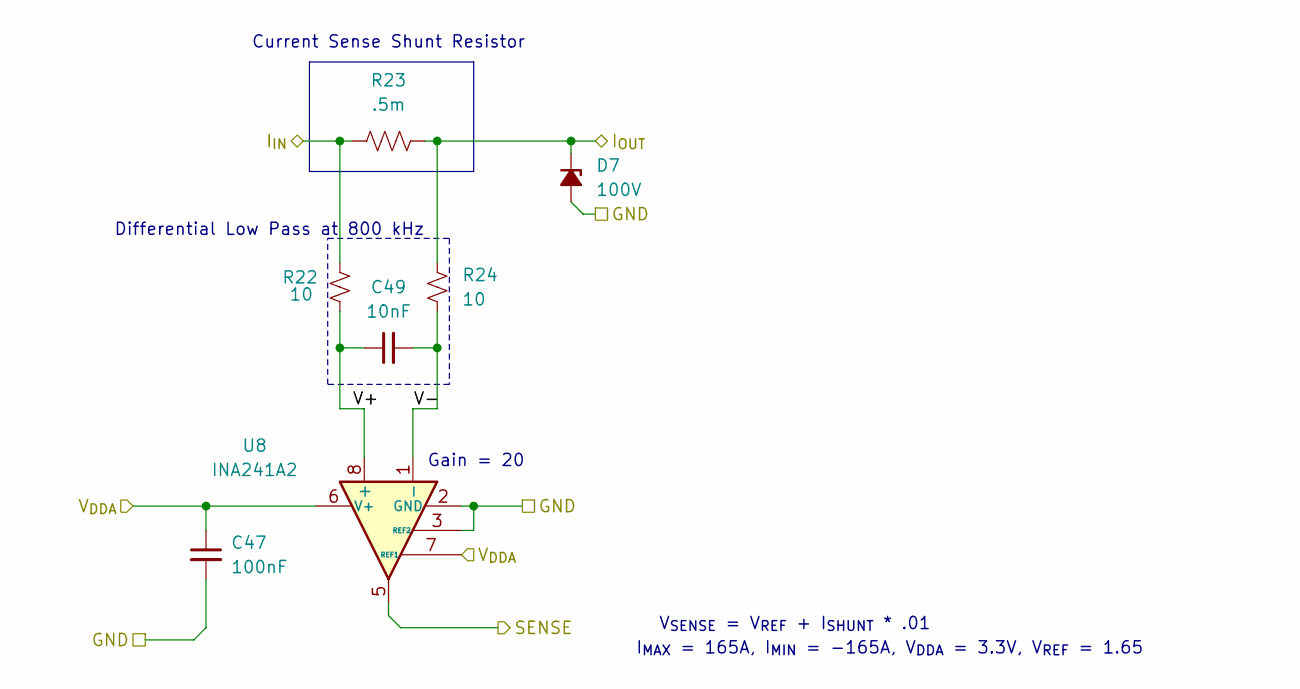
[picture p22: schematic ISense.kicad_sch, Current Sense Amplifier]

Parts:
C47: 100nF; C_0402_1005Metric; Rating 6.3V; Manufacturer_Part_Number CGA0603X7R104K500JT
C49: 10nF; C_0402_1005Metric; Rating 5V; Manufacturer_Part_Number CSA0603X7R103K500JT
D7: 100V; D_SOD-123F
R22, R24: 10; R_0402_1005Metric; Rating 100mW; Manufacturer_Part_Number RTT0310R0FTP
R23: .5m; R_2512_6332Metric; Rating 3W; Manufacturer_Part_Number ASR-M-3-0.5F
U8: INA241A2; SOT-23-8; Rating 110V; Manufacturer_Part_Number INA241A2DDFR

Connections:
/A: D7.1 (K), R23.2, R24.1; also elsewhere on the board
/GND: C47.2, D7.2 (A), U8.2 (GND), U8.3 (REF2), U8.4 (GND); also elsewhere on the board
/I_SENSE.A: U8.5; also elsewhere on the board
/Phase Current Sensors/Current Sense A/V+: C49.1, R22.2, U8.8 (+)
/Phase Current Sensors/Current Sense A/V-: C49.2, R24.2, U8.1 (-)
/SW.A: R22.1, R23.1; also elsewhere on the board
/V_{ANA}: C47.1, U8.6 (V+), U8.7 (REF1); also elsewhere on the board

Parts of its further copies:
C52, C57: 100nF; C_0402_1005Metric; Rating 6.3V; Manufacturer_Part_Number CGA0603X7R104K500JT
C54, C59: 10nF; C_0402_1005Metric; Rating 5V; Manufacturer_Part_Number CSA0603X7R103K500JT
D8, D9: 100V; D_SOD-123F
R25, R27, R28, R30: 10; R_0402_1005Metric; Rating 100mW; Manufacturer_Part_Number RTT0310R0FTP
R26, R29: .5m; R_2512_6332Metric; Rating 3W; Manufacturer_Part_Number ASR-M-3-0.5F
U9, U10: INA241A2; SOT-23-8; Rating 110V; Manufacturer_Part_Number INA241A2DDFR

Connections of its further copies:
/B: D8.1 (K), R26.2, R27.1; also elsewhere on the board
/C: D9.1 (K), R29.2, R30.1; also elsewhere on the board
/GND: C52.2, C57.2, D8.2 (A), D9.2 (A), U9.2 (GND), U9.3 (REF2), U9.4 (GND), U10.2 (GND), U10.3 (REF2), U10.4 (GND); also elsewhere on the board
/I_SENSE.B: U9.5; also elsewhere on the board
/I_SENSE.C: U10.5; also elsewhere on the board
/Phase Current Sensors/Current Sense B/V+: C54.1, R25.2, U9.8 (+)
/Phase Current Sensors/Current Sense B/V-: C54.2, R27.2, U9.1 (-)
/Phase Current Sensors/Current Sense C/V+: C59.1, R28.2, U10.8 (+)
/Phase Current Sensors/Current Sense C/V-: C59.2, R30.2, U10.1 (-)
/SW.B: R25.1, R26.1; also elsewhere on the board
/SW.C: R28.1, R29.1; also elsewhere on the board
/V_{ANA}: C52.1, C57.1, U9.6 (V+), U9.7 (REF1), U10.6 (V+), U10.7 (REF1); also elsewhere on the board

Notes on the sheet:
Current Sense Shunt Resistor
Differential Low Pass at 800 kHz
V_{SENSE} = V_{REF} + I_{SHUNT} * .01
Gain = 20
I_{MAX} = 165A, I_{MIN} = -165A, V_{DDA} = 3.3V, V_{REF} = 1.65

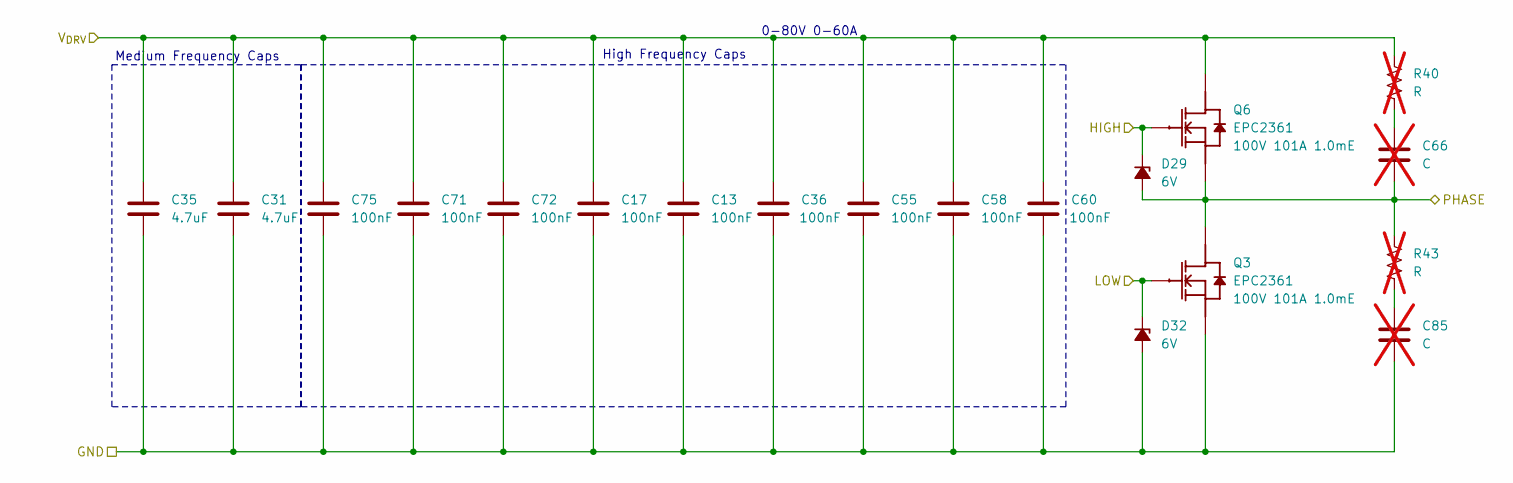
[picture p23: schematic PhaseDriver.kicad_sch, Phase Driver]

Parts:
C13, C17, C36, C55, C58, C60, C71, C72, C75: 100nF; C_0603_1608Metric; Rating 100V; Manufacturer_Part_Number CGA0603X7R104K101JT
C31, C35: 4.7uF; C_1210_3225Metric; Rating 100V
C66, C85: C; C_0603_1608Metric; Manufacturer_Part_Number N/A; not fitted
D29, D32: 6V; D_SOD-882; Rating 1A; Manufacturer_Part_Number MMSZ5233BS-7-F
Q3: EPC2361; D0606F_100V; Manufacturer_Part_Number EPC2302
Q6: EPC2361; D0606F_100V; Manufacturer_Part_Number EPC2361
R40, R43: R; R_0603_1608Metric; Manufacturer_Part_Number N/A; not fitted

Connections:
/CH: D29.1 (K), Q6.1 (G); also elsewhere on the board
/CL: D32.1 (K), Q3.1 (G); also elsewhere on the board
/GND: C13.2, C17.2, C31.2, C35.2, C36.2, C55.2, C58.2, C60.2, C71.2, C72.2, C75.2, C85.2, D32.2 (A), Q3.2 (S), Q3.4 (S), Q3.6 (S); also elsewhere on the board
/SW.C: C66.2, D29.2 (A), Q3.3 (D), Q3.5 (D), Q3.7 (D), Q6.2 (S), Q6.4 (S), Q6.6 (S), R43.1; also elsewhere on the board
/V_{BATT}: C13.1, C17.1, C31.1, C35.1, C36.1, C55.1, C58.1, C60.1, C71.1, C72.1, C75.1, Q6.3 (D), Q6.5 (D), Q6.7 (D), R40.1; also elsewhere on the board
unnamed: C66.1, R40.2
unnamed: C85.1, R43.2

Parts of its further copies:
C4, C5, C10, C14, C16, C20, C22, C25, C30, C33, C46, C48, C50, C51, C53, C70, C73, C74: 100nF; C_0603_1608Metric; Rating 100V; Manufacturer_Part_Number CGA0603X7R104K101JT
C28, C29, C32, C34: 4.7uF; C_1210_3225Metric; Rating 100V
C56, C61, C83, C84: C; C_0603_1608Metric; Manufacturer_Part_Number N/A; not fitted
D27, D28, D30, D31: 6V; D_SOD-882; Rating 1A; Manufacturer_Part_Number MMSZ5233BS-7-F
Q1, Q2: EPC2361; D0606F_100V; Manufacturer_Part_Number EPC2302
Q4, Q5: EPC2361; D0606F_100V; Manufacturer_Part_Number EPC2361
R38, R39, R41, R42: R; R_0603_1608Metric; Manufacturer_Part_Number N/A; not fitted

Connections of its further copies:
/AH: D27.1 (K), Q4.1 (G); also elsewhere on the board
/AL: D30.1 (K), Q1.1 (G); also elsewhere on the board
/BH: D28.1 (K), Q5.1 (G); also elsewhere on the board
/BL: D31.1 (K), Q2.1 (G); also elsewhere on the board
/GND: C4.2, C5.2, C10.2, C14.2, C16.2, C20.2, C22.2, C25.2, C28.2, C29.2, C30.2, C32.2, C33.2, C34.2, C46.2, C48.2, C50.2, C51.2, C53.2, C70.2, C73.2, C74.2, C83.2, C84.2, D30.2 (A), D31.2 (A), Q1.2 (S), Q1.4 (S), Q1.6 (S), Q2.2 (S), Q2.4 (S), Q2.6 (S); also elsewhere on the board
/SW.A: C56.2, D27.2 (A), Q1.3 (D), Q1.5 (D), Q1.7 (D), Q4.2 (S), Q4.4 (S), Q4.6 (S), R41.1; also elsewhere on the board
/SW.B: C61.2, D28.2 (A), Q2.3 (D), Q2.5 (D), Q2.7 (D), Q5.2 (S), Q5.4 (S), Q5.6 (S), R42.1; also elsewhere on the board
/V_{BATT}: C4.1, C5.1, C10.1, C14.1, C16.1, C20.1, C22.1, C25.1, C28.1, C29.1, C30.1, C32.1, C33.1, C34.1, C46.1, C48.1, C50.1, C51.1, C53.1, C70.1, C73.1, C74.1, Q4.3 (D), Q4.5 (D), Q4.7 (D), Q5.3 (D), Q5.5 (D), Q5.7 (D), R38.1, R39.1; also elsewhere on the board
unnamed: C56.1, R38.2
unnamed: C61.1, R39.2
unnamed: C83.1, R41.2
unnamed: C84.1, R42.2

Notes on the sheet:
0-80V 0-60A
High Frequency Caps
Medium Frequency Caps

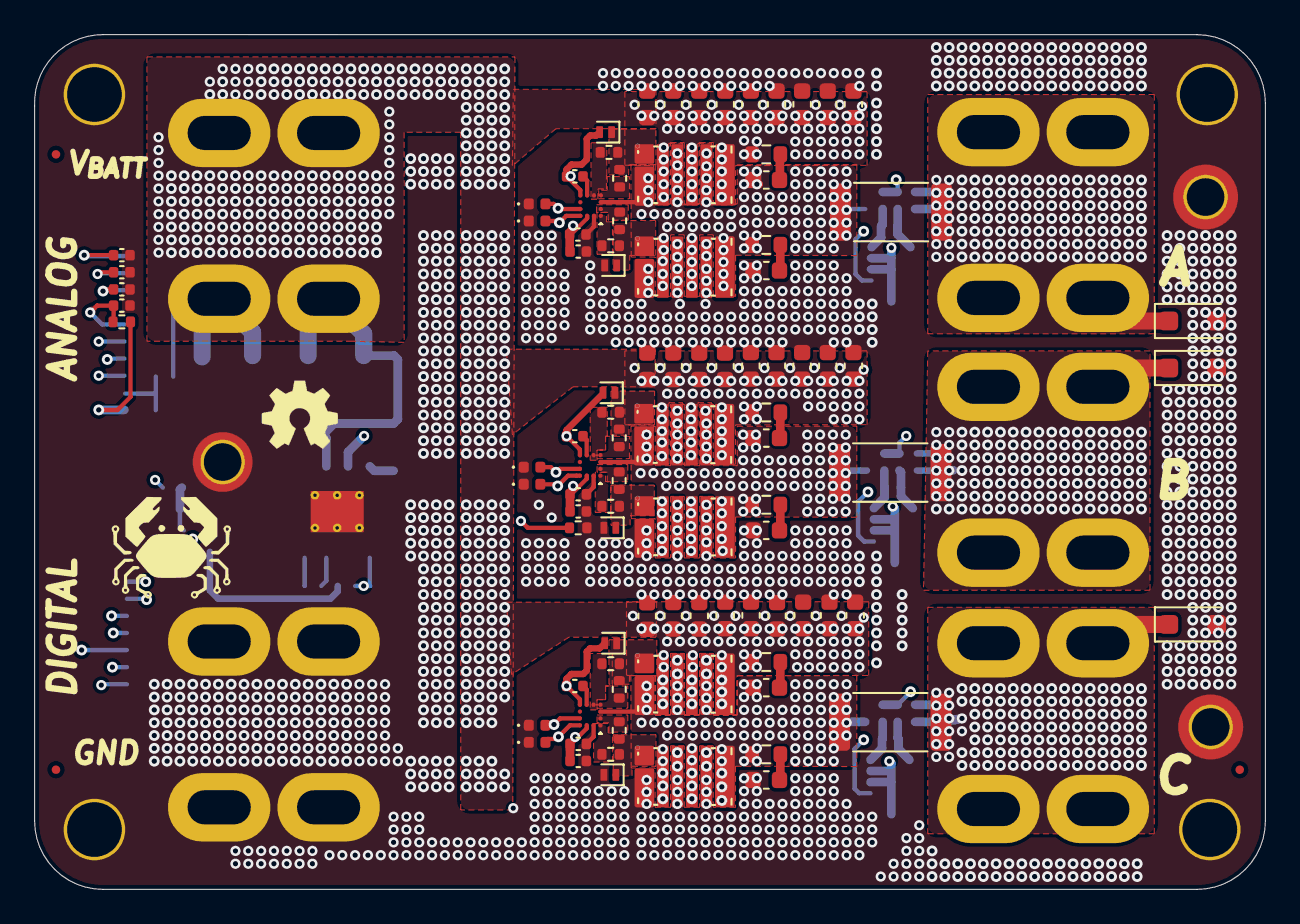
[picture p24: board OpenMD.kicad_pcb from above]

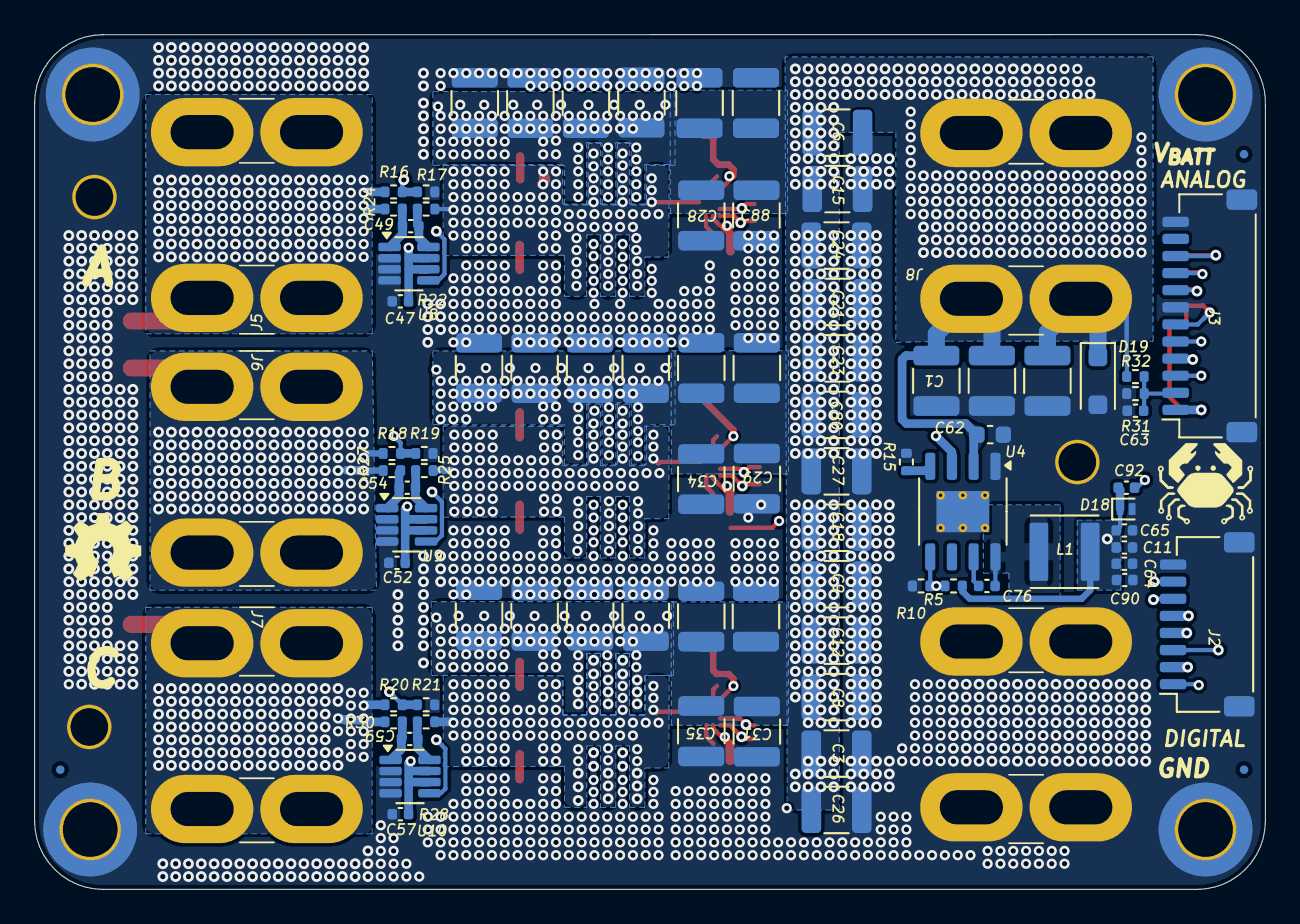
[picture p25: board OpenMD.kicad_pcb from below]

Board: 6 copper layers, 72.0 x 50.0 mm, 193 parts (93 on the bottom side), 62 nets.

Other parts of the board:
SYM1#2: Logo_Open_Hardware_Large; OSHW-Symbol_8.9x8mm_SilkScreen

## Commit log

2024-05-19 first revision
    [CurrentSensors.kicad_sch, DriverCurrentSense.kicad_sch, Drivers.kicad_sch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]
2024-05-20 added license and almost ready for prod
    [DriverCurrentSense.kicad_sch, Drivers.kicad_sch, GateDriver.kicad_sch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]
2024-06-05 first fab run
    [CurrentSensors.kicad_sch, DriverCurrentSense.kicad_sch, Drivers.kicad_sch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]
2024-06-05 Production round 1
    [Drivers.kicad_sch, OpenMD.kicad_pcb, PhaseDriver.kicad_sch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]
2024-06-06 added docs
    [CurrentSensors.kicad_sch, OpenMD.kicad_pcb]
2024-06-06 added ESD protection
    [CurrentSensors.kicad_sch, GateDriver.kicad_sch, ISense.kicad_sch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]
2024-06-06 add context
    [CurrentSensors.kicad_sch, ISense.kicad_sch, OpenMD.kicad_pcb]
2024-06-08 more powerful version
    [PhaseDriver.kicad_sch]
2024-06-09 adjusted according to Reddit feedback
    Still needs TVS adjusted
    [GateDriver.kicad_sch, ISense.kicad_sch, OpenMD.kicad_sch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]
2024-06-09 added all changes from Reddit
    [GateDriver.kicad_sch, ISense.kicad_sch, OpenMD.kicad_sch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]
2024-06-18 Removed Hall Sensors for Scalability
    [OpenMD.kicad_sch, PhaseDriver.kicad_sch]
2024-06-19 updates to make better
    [Drivers.kicad_sch, GateDriver.kicad_sch, ISense.kicad_sch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]
2024-06-22 moved amps to back
    [GateDriver.kicad_sch, ISense.kicad_sch, OpenMD.kicad_pcb]
2024-06-23 fixed grounding issues
    [OpenMD.kicad_pcb]
2024-06-23 update fab layers
    [OpenMD.kicad_pcb]
2024-07-05 revision 2
    [GateDriver.kicad_sch, ISense.kicad_sch, OpenMD.kicad_pcb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]
2024-07-21 add heatspreader
    [OpenMD.kicad_pcb]
2024-08-31 next generation
    [Drivers.kicad_sch, OpenMD.kicad_pcb, PhaseDriver.kicad_sch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]
2024-12-19 added more capacitance
    [CurrentSensors.kicad_sch, Drivers.kicad_sch, GateDriver.kicad_sch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]
